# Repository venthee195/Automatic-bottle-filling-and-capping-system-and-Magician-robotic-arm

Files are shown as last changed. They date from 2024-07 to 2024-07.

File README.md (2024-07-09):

<p align="center">
 <h1 align="center">Design and build a bottle processing system using S7-1200 and Magician robotic arm </h1>
</p>

# Introduction
This project involves the design and construction of a system for filling, capping, and arranging glass bottles. The system employs a Magician robotic arm to organize the bottles into a 3x3 grid within a square container. The manufacturing line, equipped with conveyors, pumps, and pneumatic cylinders, is responsible for the filling and capping of the bottles.

The system is controlled by a Siemens SIMATIC S7-1200 CPU 1214C PLC, which also manages the Mitsubishi AC Servo MR-J3 motors. Despite the differences between the two brands, successful integration has been achieved. The PLC is capable of reading the AC Servo’s absolute encoder, enabling the robot to automatically home itself when powered on. This simplifies the initialization process and enhances the overall efficiency of the system.

# System design and construction
Design the whole system, we need a reliable tool that can connect all the parts. That’s why we use SolidWorks 2022 It helps us complete and integrate each stage smoothly.
This part talks about the designs of each part of a system that fills, seals, and caps bottles. We’ll look at the design of the Magician Robotic Arm in Section 3.2.3.
Figure 3-10 presents an overview of the motors’ positions in the system. Each component represents a stage in the production line.

The hardware of the system includes: control devices (PLC, relay), actuators, motors, conveyors, pneumatic cylinders, Camera IMC-3616UC, sensors.

<p align="center">
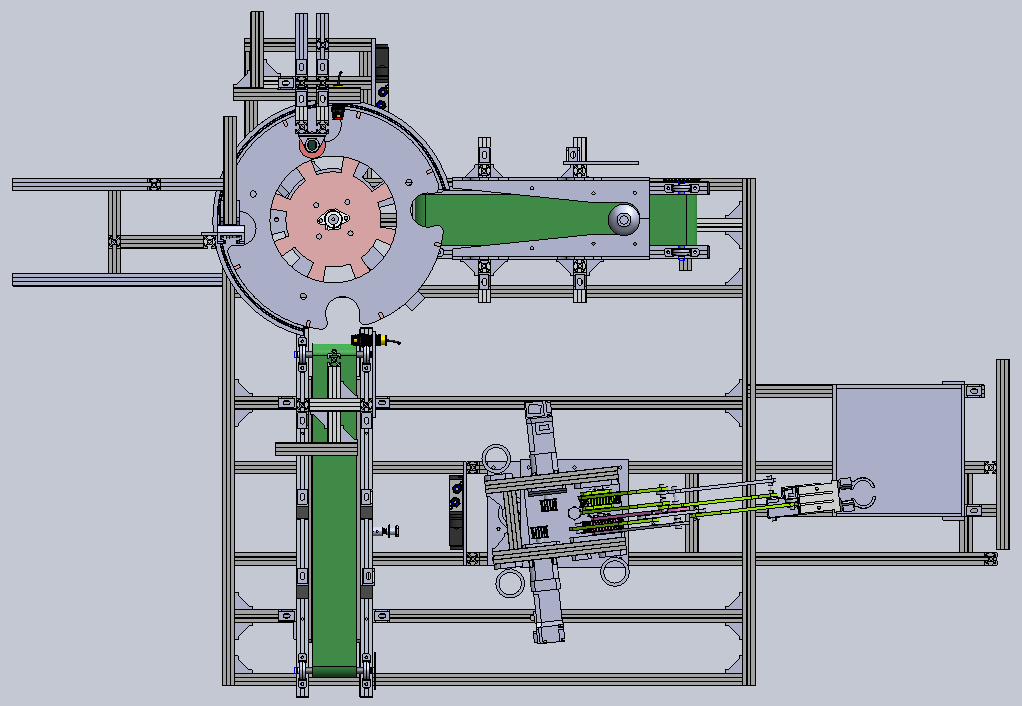
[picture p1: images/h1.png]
  <br/>
  <i>Top view of the system</i>
</p>
<p align="center">
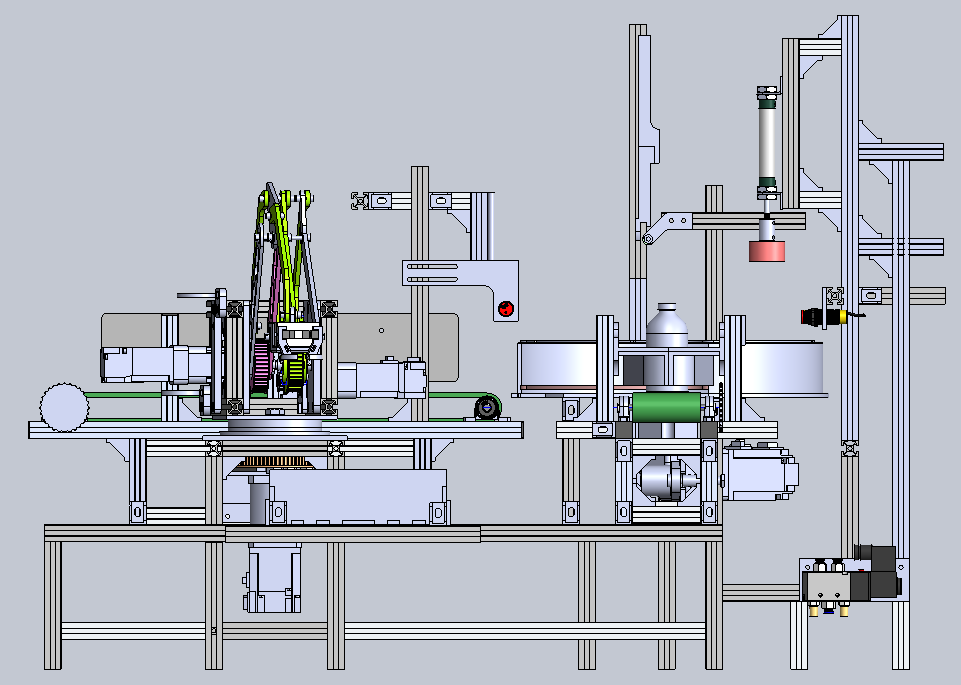
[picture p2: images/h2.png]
  <br/>
  <i>Front view of the system</i>
</p>

Overview of the project:

h3

Design of the Electrical cabinet:

<p align="center">
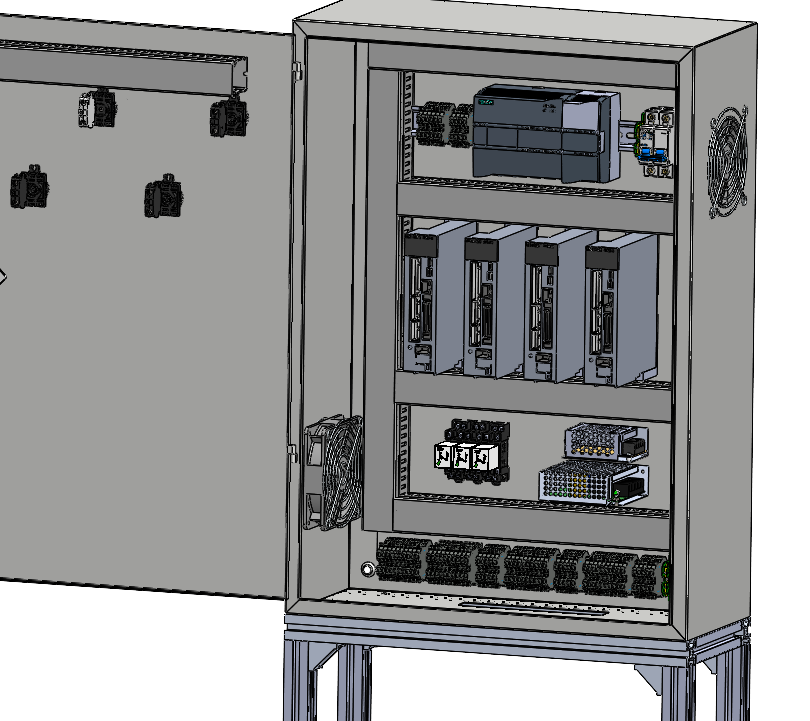
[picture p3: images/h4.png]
  <br/>
  <i> Left side view of cabinet</i>
</p>
<p align="center">
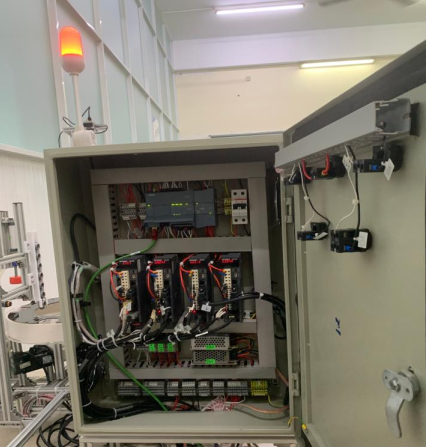
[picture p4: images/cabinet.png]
  <br/>
  <i> Overview of the actual electrical cabinet</i>
</p>
Programmable Logic Controller (PLC): This is the main control unit, responsible for automating various functions.

Circuit Breakers (CB): These are located at the top of the cabinet and protect the circuit from damage caused by excess current from an overload or short circuit.

Servo Drive: Positioned in the middle of the cabinet, this controls the operation of the servo motor.
Intermediate Relays: These devices control the power circuits.

AC to DC Converters: There are two converters, one for 12V and another for 24V, which convert alternating current (AC) to direct current (DC).

Terminal Blocks: These secure and/or terminate multiple wire connections.

Fans: Two 12V fans, each running at 1500 RPM and measuring 12x12 cm, are installed for cooling purposes.

<p align="center">
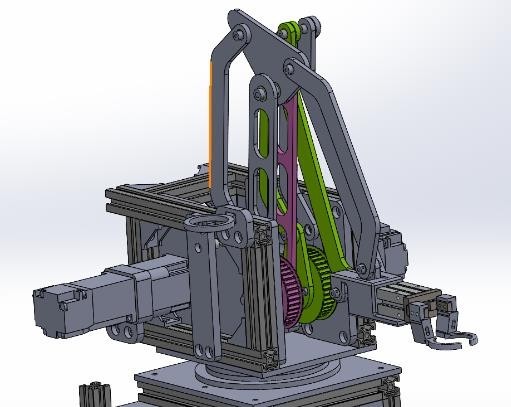
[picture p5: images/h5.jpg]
  <br/>
  <i>Magician Robot Arm model by SolidWorks</i>
</p>

# Control interface design
The interface is designed by the team using the C# programming language.

<p align="center">
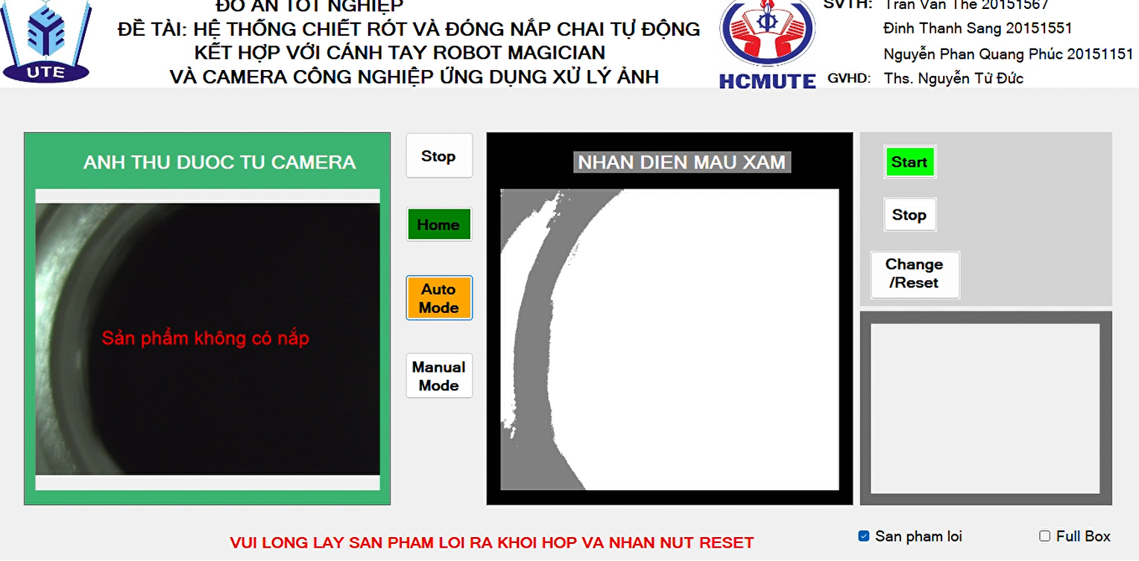
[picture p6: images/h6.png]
  <br/>
  <i>Product interface without cover</i>
</p>

<p align="center">
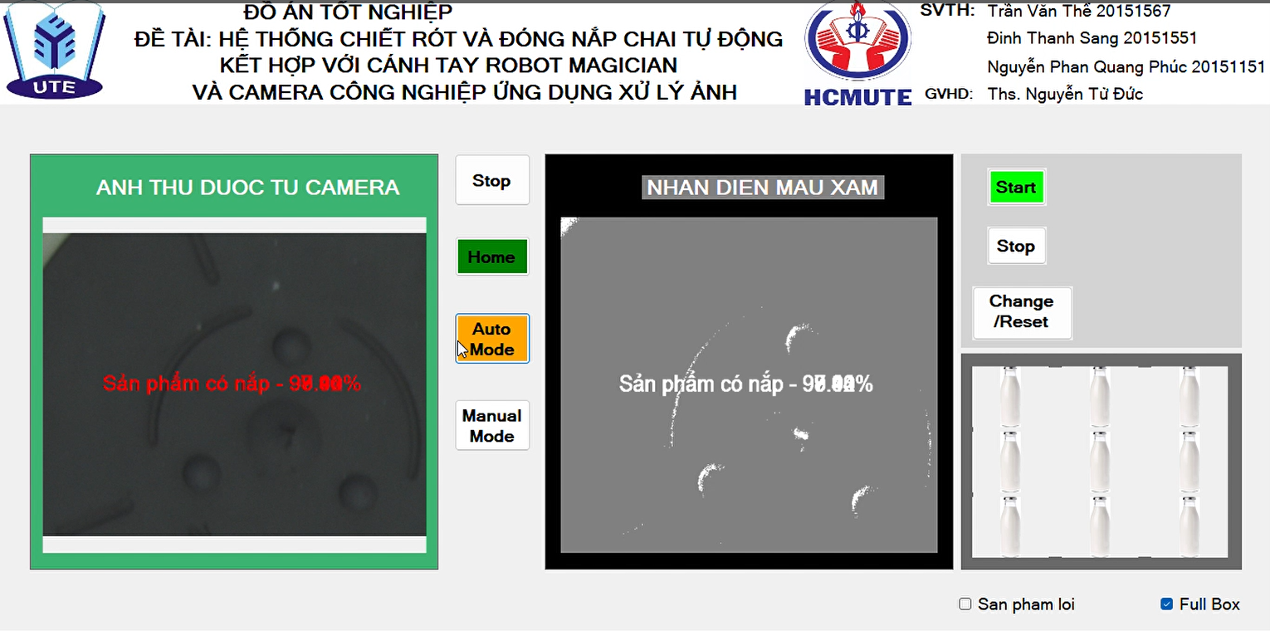
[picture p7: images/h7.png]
  <br/>
  <i>The product interface has a cap and a filled bottle</i>
</p>

# The system wiring diagram

<p align="center">
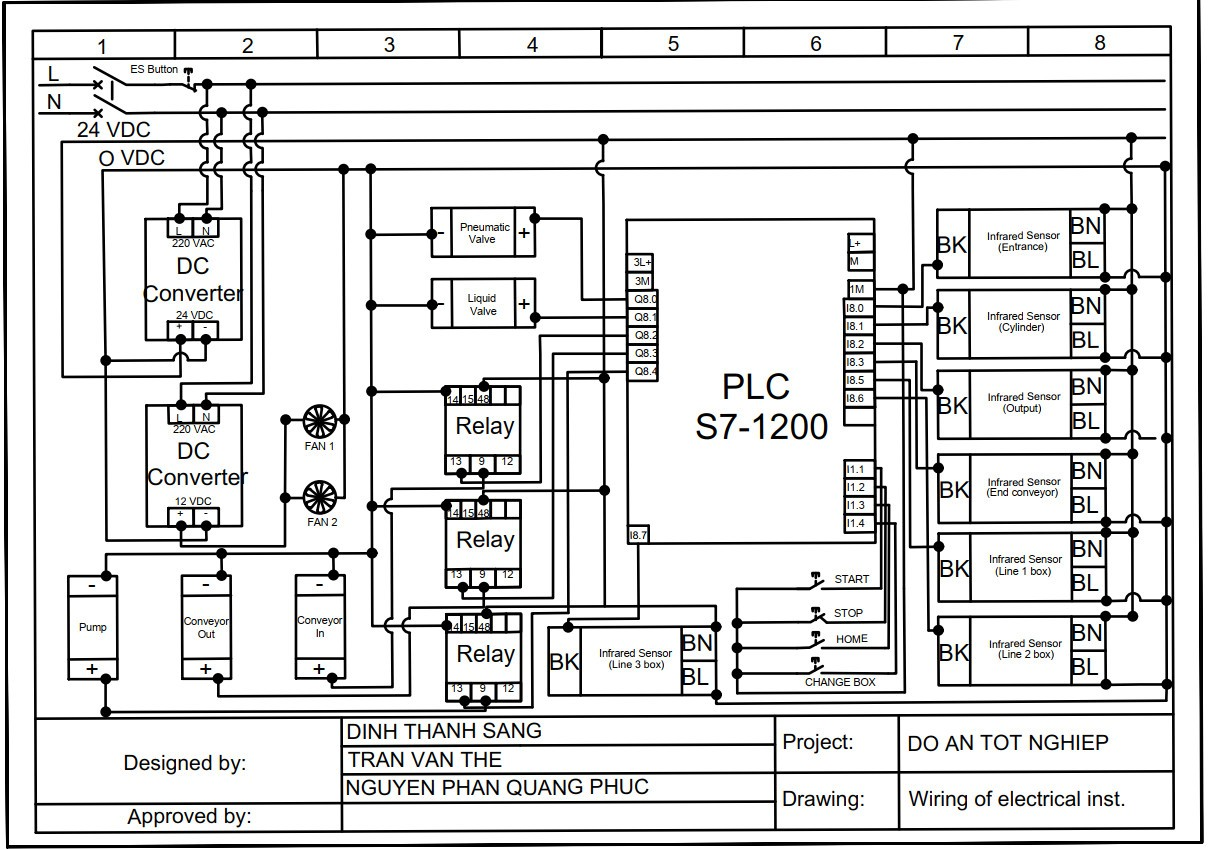
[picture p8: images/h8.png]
  <br/>
  <i>Wiring diagram of other actuators and sensors</i>
</p>

<p align="center">
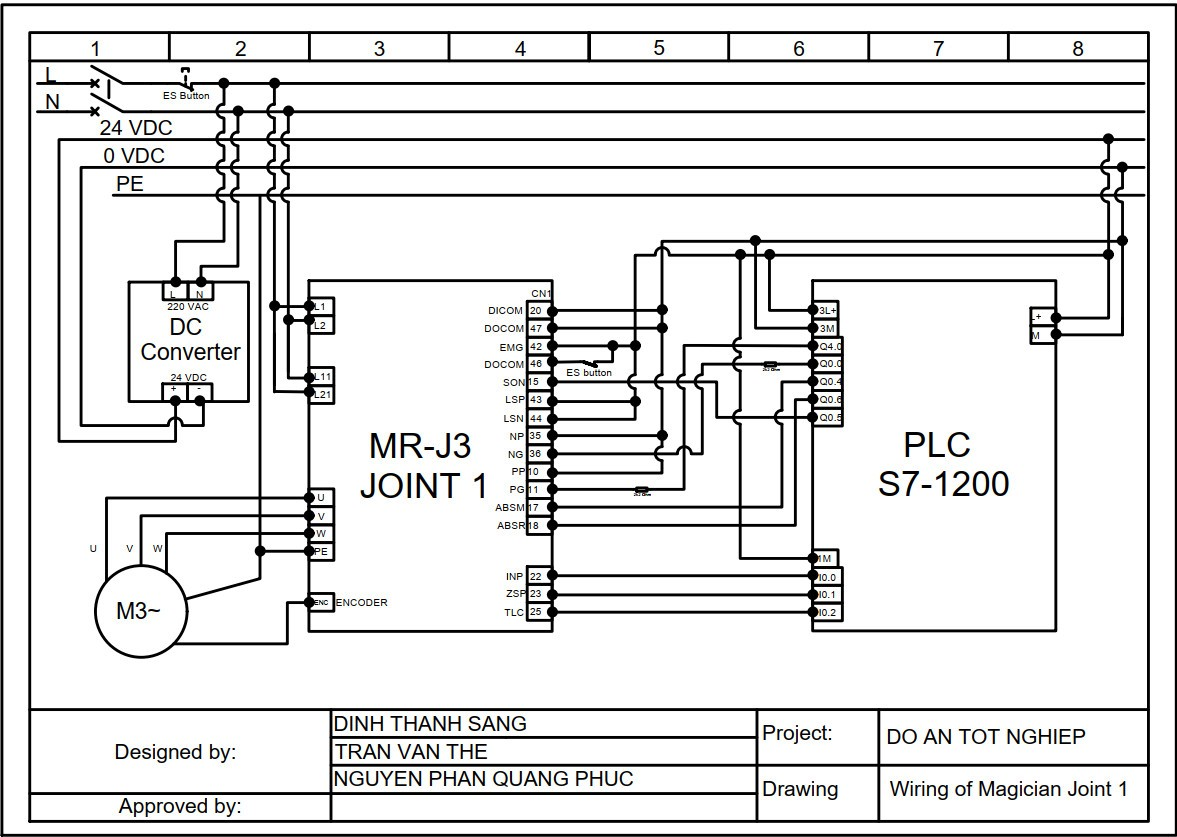
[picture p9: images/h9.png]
  <br/>
  <i>Wiring diagram for Joint 1 of the robotic arm</i>
</p>
<p align="center">
  <img src="images/h10.png width=600><br/>
  <i>Wiring diagram for Joint 2 of the robotic arm</i>
</p>
<p align="center">
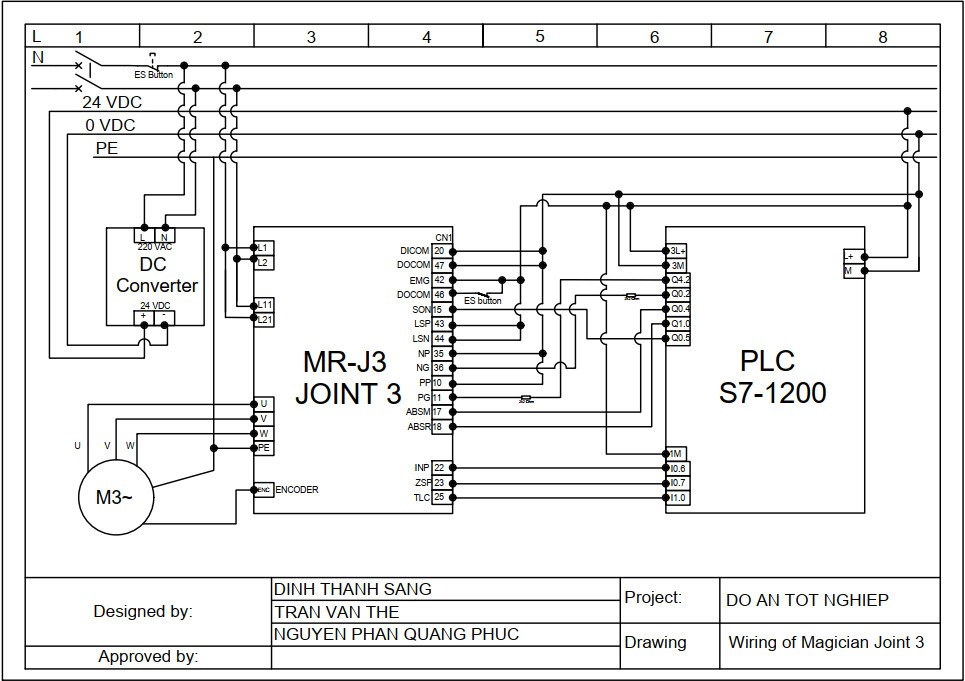
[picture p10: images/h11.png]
  <br/>
  <i>Wiring diagram for Joint 3 of the robotic arm</i>
</p>

 # 
# Experimental results
Initially, empty bottles are placed on the input conveyor and pushed towards the end of the conveyor to fill water into the bottles
<p align="center">
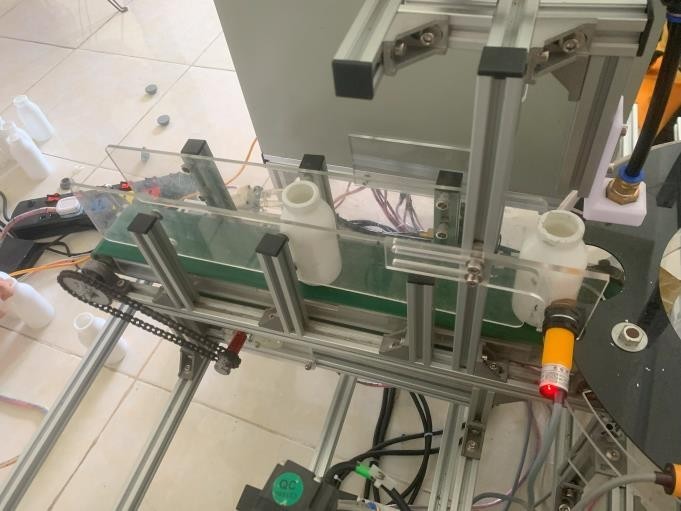
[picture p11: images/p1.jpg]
  <br/>
  <i>Bottles in the input conveyor</i>
</p>

<p align="center">
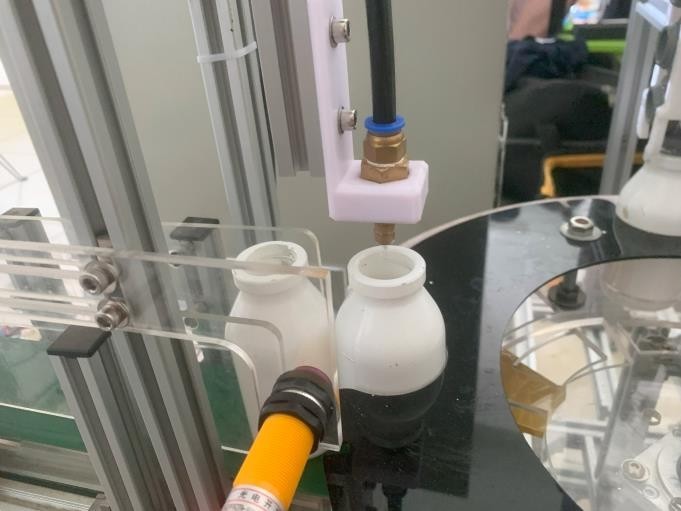
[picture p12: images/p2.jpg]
  <br/>
  <i> Filling water into a bottle</i>
</p>

<p align="center">
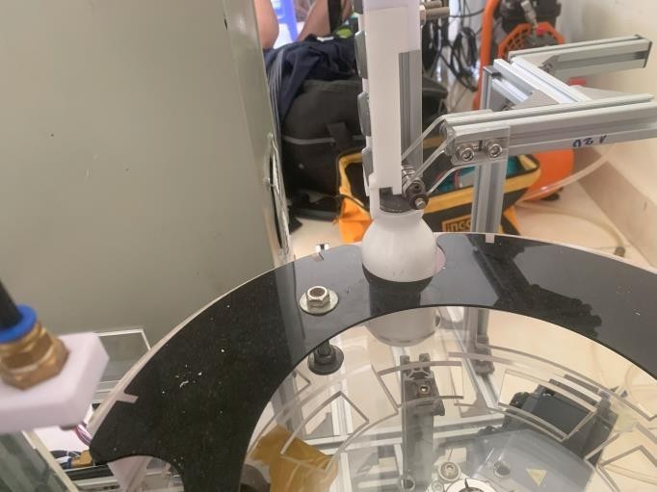
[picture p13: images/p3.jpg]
  <br/>
  <i>Capping a bottle</i>
</p>

<p align="center">
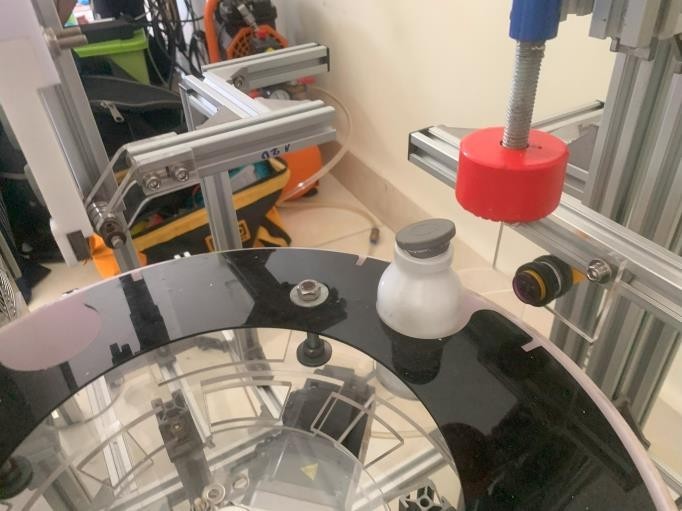
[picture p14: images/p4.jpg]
  <br/>
  <i>Cap before it is capped</i>
</p>
<p align="center">
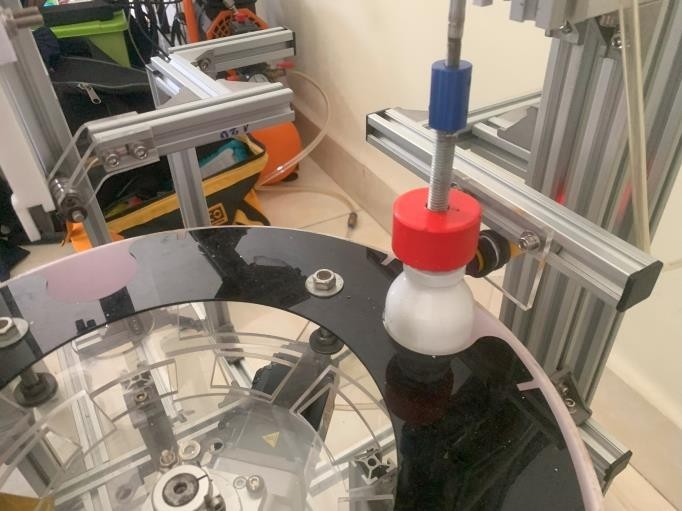
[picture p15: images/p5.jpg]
  <br/>
  <i>Pneumatic cylinder is capping the bottle</i>
</p>

<p align="center">
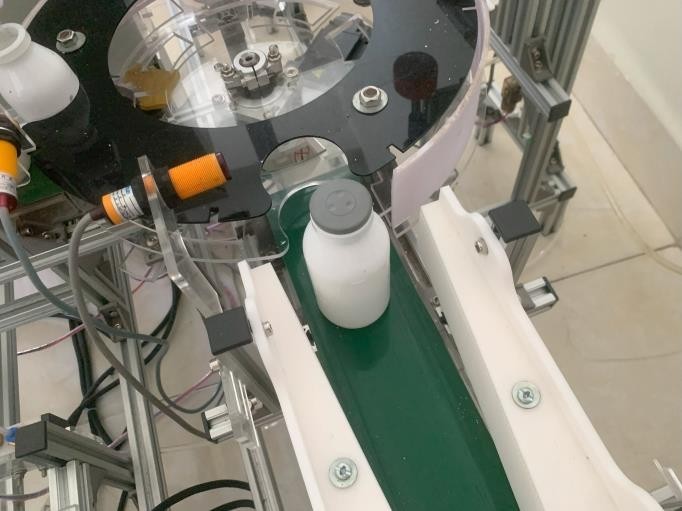
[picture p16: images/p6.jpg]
  <br/>
  <i>Bottles are delivered to the output conveyor</i>
</p>
<p align="center">
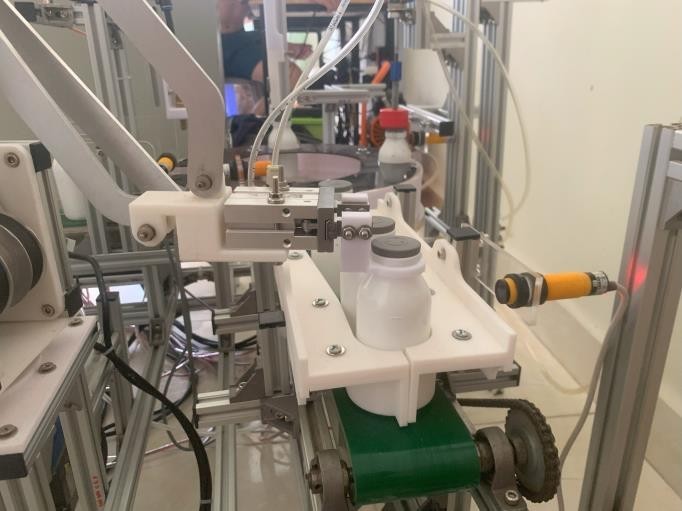
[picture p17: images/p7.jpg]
  <br/>
  <i>A pneumatic cylinder grips bottle</i>
</p>
<p align="center">
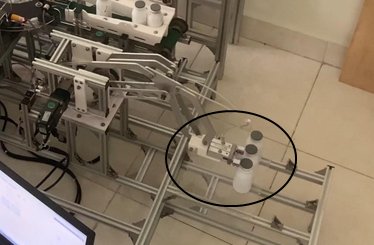
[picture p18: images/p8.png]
  <br/>
  <i>Robotics Arm puts the bottles into the storage</i>
</p>

# Video
For more detail, you can watch the Video show how the system operating: https://youtu.be/p6lmQUOT4Mk?si=QC_-EGU05_skhJYb

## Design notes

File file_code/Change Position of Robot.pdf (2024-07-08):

## Totally Integrated Automation Portal

# Change Position of Robot [FC6]

## Change Position of Robot Properties General

Name | Change Position of Robot | Number | 6 | Type | FC | Language | LAD
Numbering | Automatic

## Information

Title | | Author | Comment | Family
Version | 0.1 | User-defined ID
Name | Data type | Default value | Comment

## Input Output InOut Temp Constant Return

Change Position of Robot | Void

# Network 1: STATE 1 ON

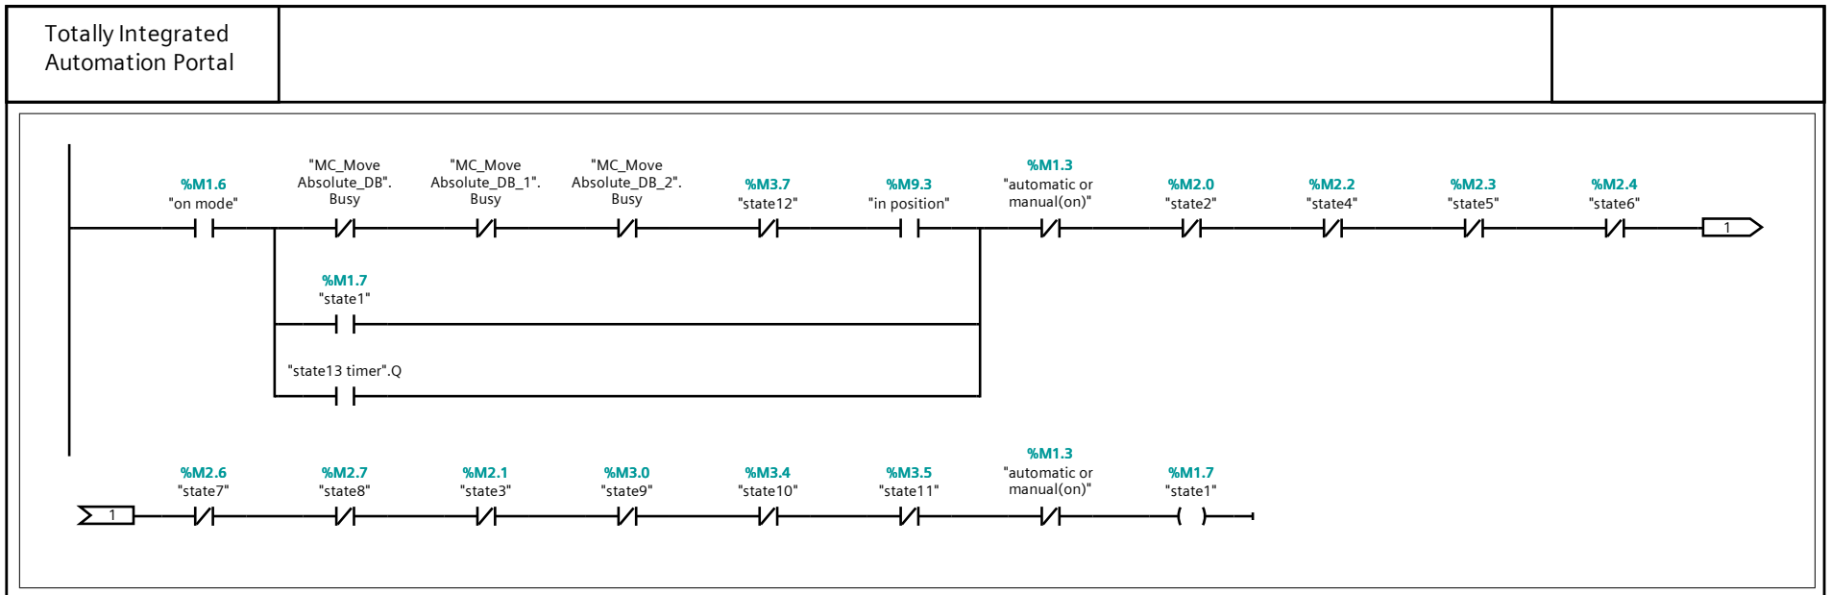
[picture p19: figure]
Automation Portal; "on mode"; "MC_Move Absolute_DB". Busy; "MC_Move Absolute_DB_1". Busy; "MC_Move Absolute_DB_2".; Busy; "state12"; "in position"; "automatic or; manual(on)"; "state2"; "state4"; "state5"; "state6"; "state7"; "state8"; "state3"; "state9"; "state10"; "state11"; "state1"; "state13 timer".Q

# Network 2: Vi tri cua state1

MOVE

MOVE

MOVE

"state1"

%M1.7

450.0
"px"

%MD100

0.0
"py"

%MD104

30.0
"pz"

%MD108

EN
IN

ENO

OUT1

EN
IN

ENO

OUT1

EN
IN

ENO

OUT1

EN
IN

ENO

OUT1

EN
IN

ENO

OUT1

EN
IN

ENO

# OUT1 Network 3:

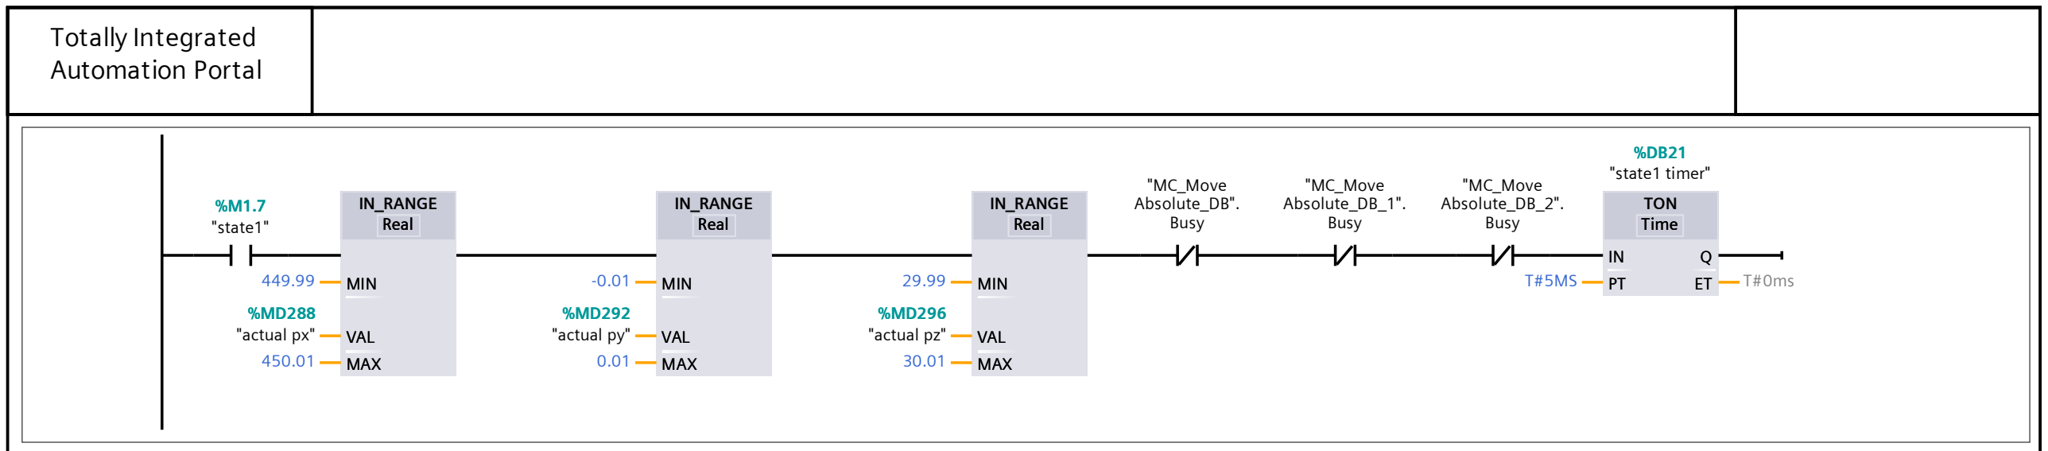
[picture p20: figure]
Automation Portal; IN_RANGE Real; TON; "state1"; Time; "actual px"; "actual py"; "actual pz"; "MC_Move Absolute_DB". Busy; "MC_Move Absolute_DB_1". Busy; "MC_Move Absolute_DB_2". Busy; "state1 timer"; %DB21 MIN; T#0ms VAL MAX; Real; MIN; VAL MAX; Time MIN
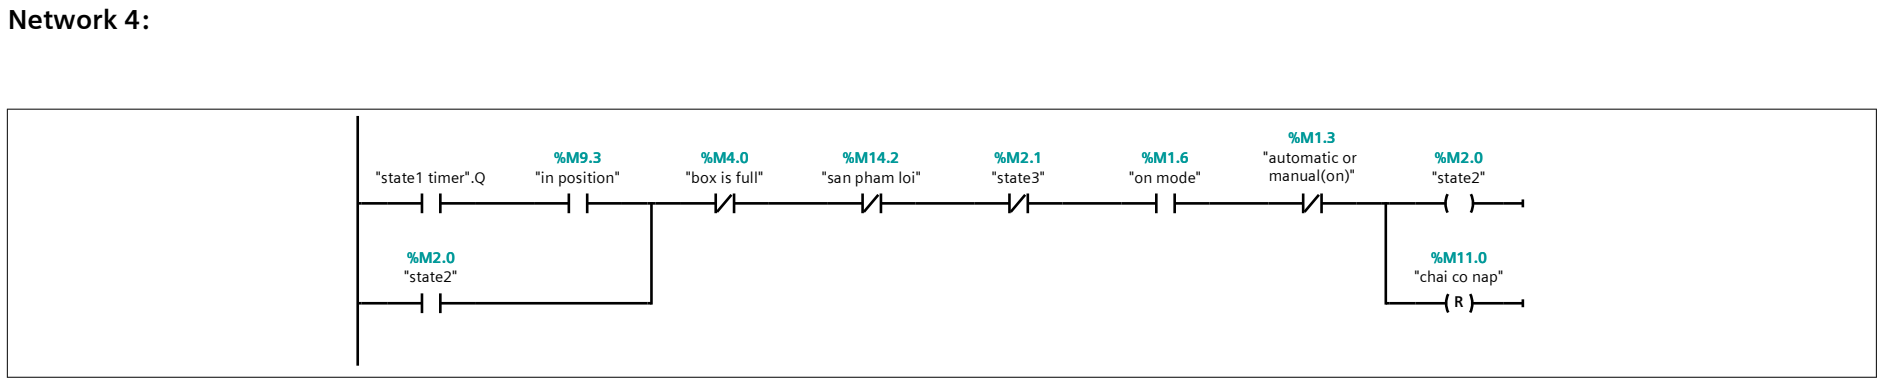
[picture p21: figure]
Network 4:; "state1 timer".Q; "in position"; "box is full"; "san pham loi"; "state3"; "on mode"; "automatic or; manual(on)"; "state2"; "chai co nap"

# Network 5:

## Automation Portal

MOVE

MOVE

MOVE

"state2"

%M2.0

"bottle on
conveyor px"

%MD474
"px"

%MD100

"bottle on
conveyor py"

%MD478
"py"

%MD104

130.0
"pz"

%MD108

EN

IN

ENO

OUT1

EN

IN

ENO

OUT1

EN
IN

ENO

OUT1

EN

IN

ENO

OUT1

EN

IN

ENO

OUT1

EN
IN

ENO

# OUT1 Network 6:

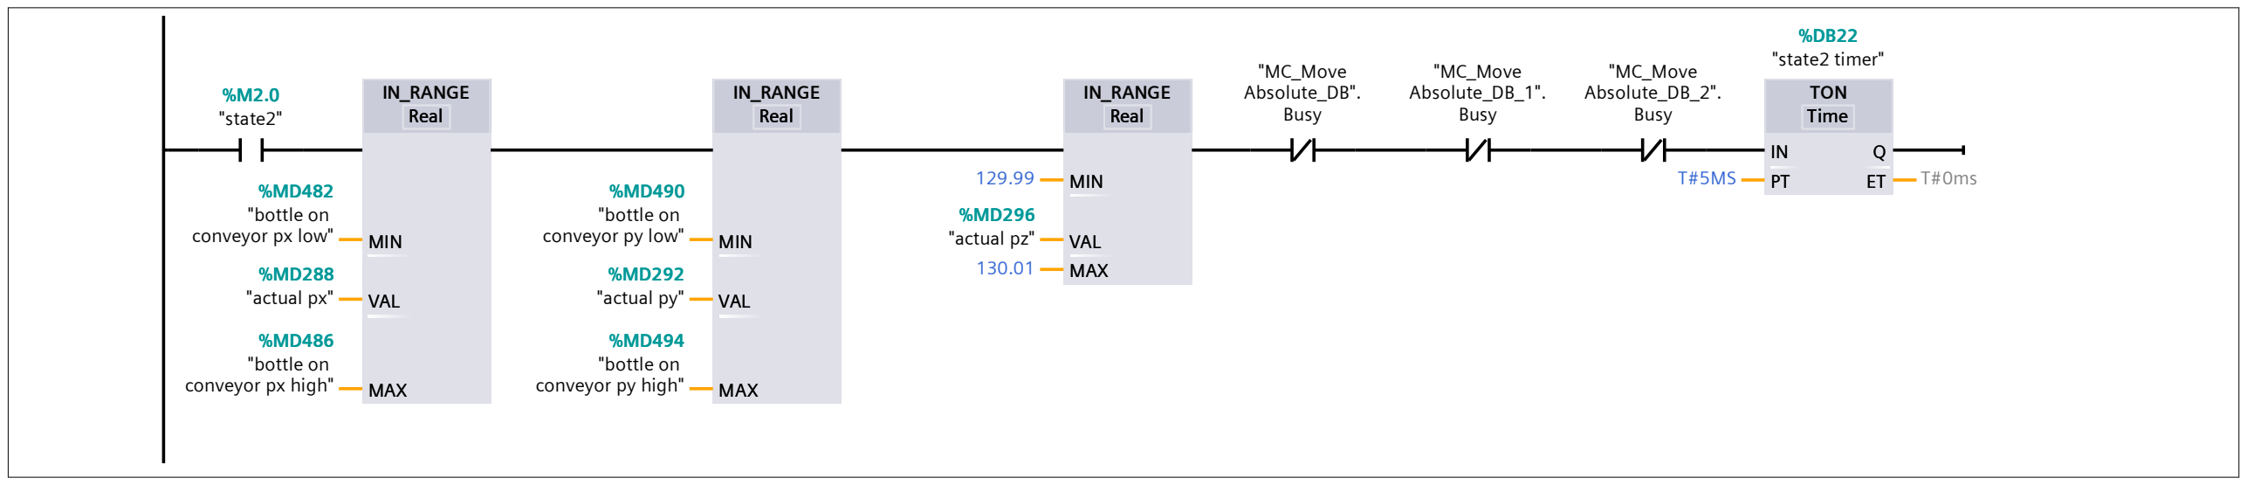
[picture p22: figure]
IN_RANGE Real; TON; "state2"; Time; "bottle on conveyor px low"; "actual px"; "bottle on conveyor px high"; "bottle on conveyor py low"; "actual py"; "bottle on conveyor py high"; "actual pz"; "MC_Move Absolute_DB". Busy; "MC_Move Absolute_DB_1". Busy; "MC_Move Absolute_DB_2". Busy; "state2 timer"; T#0ms MIN; VAL MAX; Real; MIN; Time MIN

# Network 7:

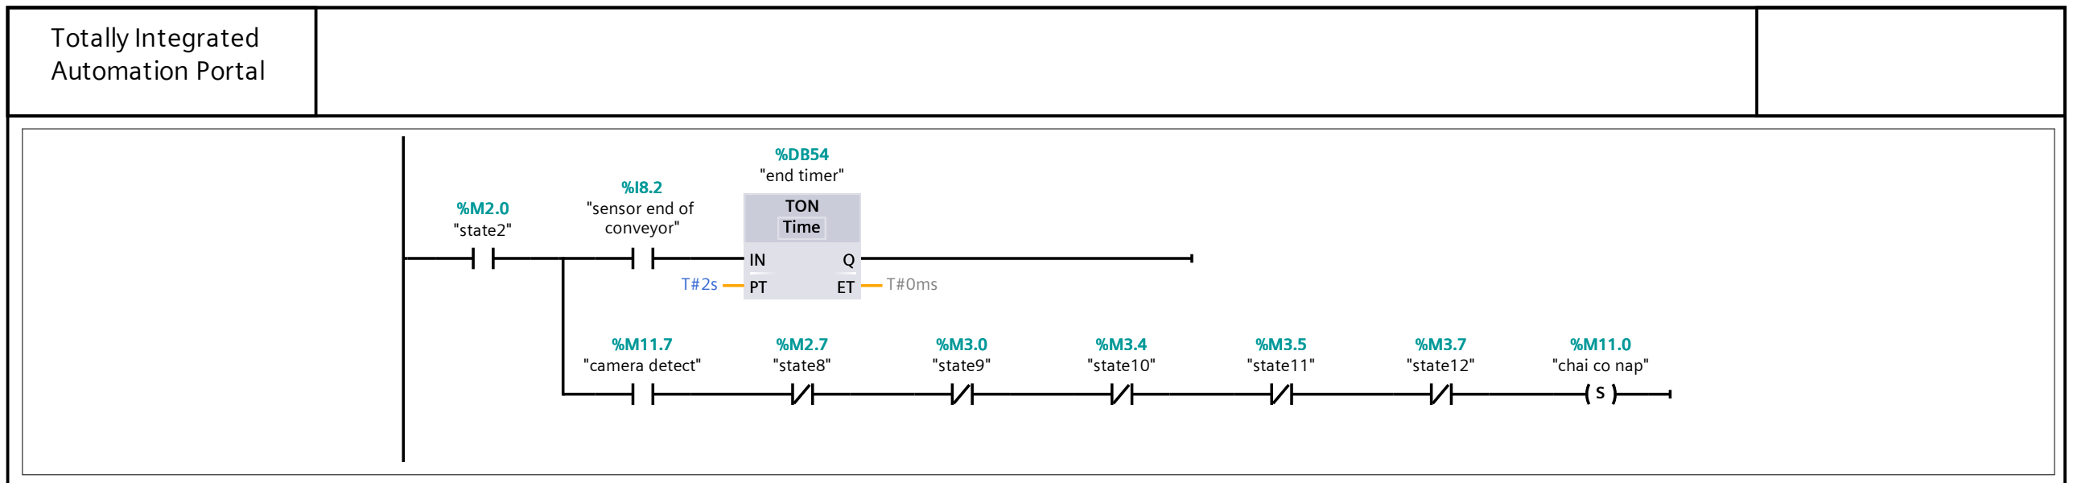
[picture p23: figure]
Automation Portal; TON Time; "state2"; "sensor end of; conveyor"; "end timer"; "camera detect"; "state8"; "state9"; "state10"; "state11"; "state12"; "chai co nap"; Time

# Network 8:

"state2 timer".Q "in position"

%M9.3
"end timer".Q | "state4"

%M2.2
"on mode"
%M1.6 | "automatic or
manual(on)"

%M1.3

"state3"

%M2.1

"state3"

%M2.1

# Network 9:

## Automation Portal

MOVE

MOVE

MOVE

"state3"

%M2.1

"bottle on
conveyor px"

%MD474
"px"

%MD100

"bottle on
conveyor py"

%MD478
"py"

%MD104

115.0
"pz"

%MD108

EN

IN

ENO

OUT1

EN

IN

ENO

OUT1

EN
IN

ENO

OUT1

EN

IN

ENO

OUT1

EN

IN

ENO

OUT1

EN
IN

ENO

# OUT1 Network 10:

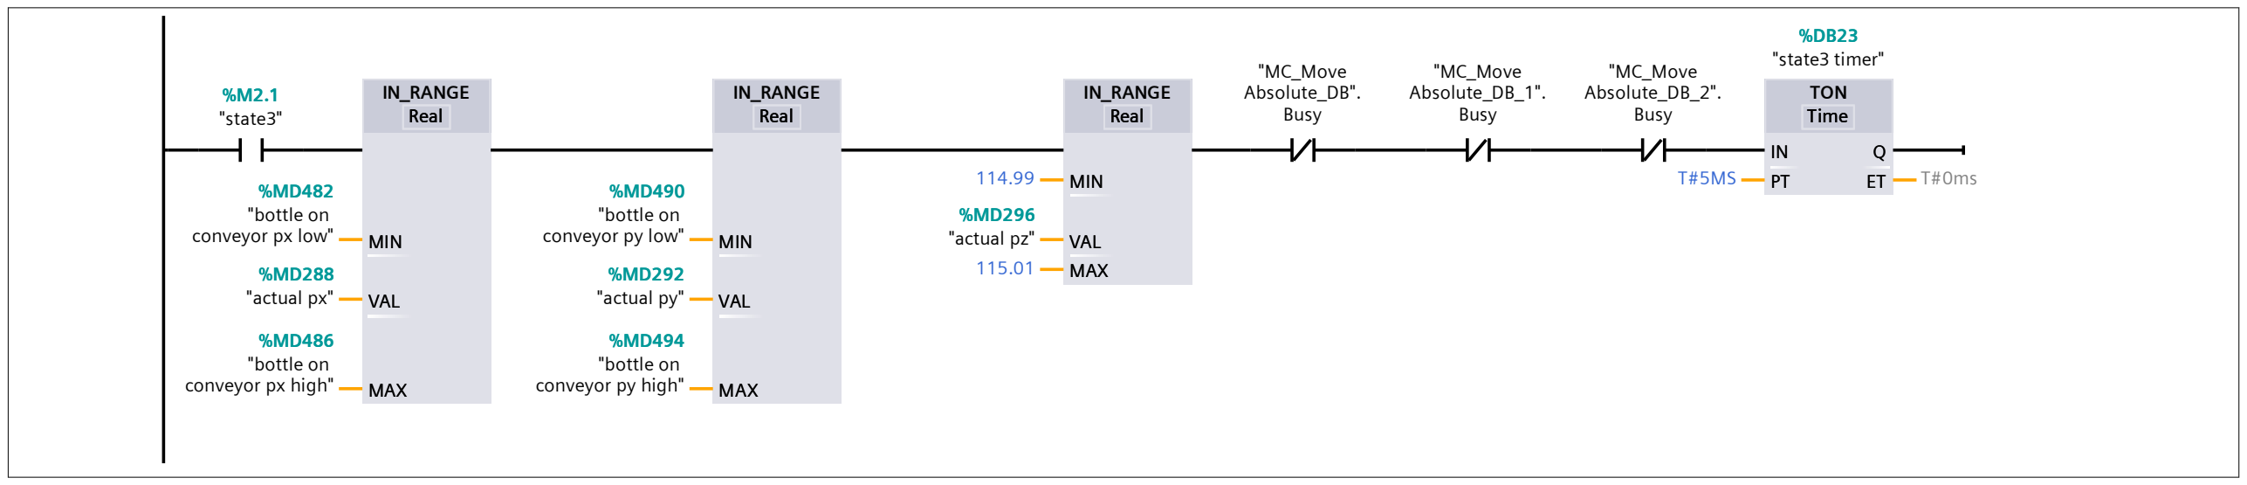
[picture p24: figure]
IN_RANGE Real; TON; "state3"; Time; "bottle on conveyor px low"; "actual px"; "bottle on conveyor px high"; "bottle on conveyor py low"; "actual py"; "bottle on conveyor py high"; "actual pz"; "MC_Move Absolute_DB". Busy; "MC_Move Absolute_DB_1". Busy; "MC_Move Absolute_DB_2". Busy; "state3 timer"; T#0ms MIN; VAL MAX; Real; MIN; Time MIN

# Network 11:

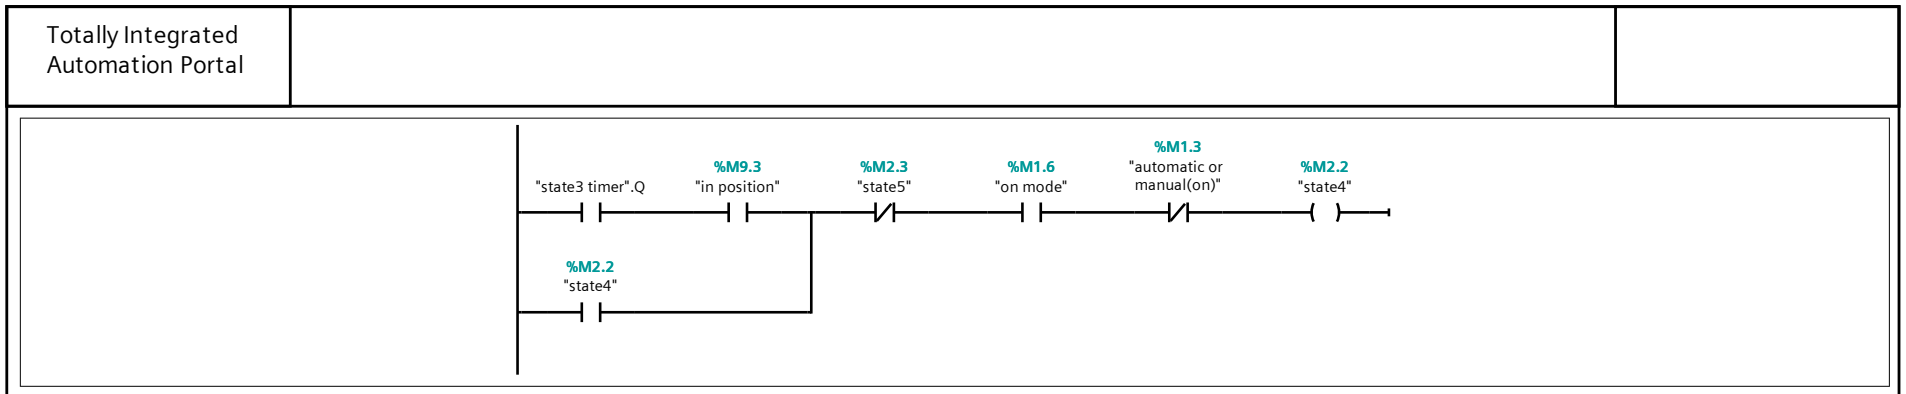
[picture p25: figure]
Automation Portal; "state3 timer".Q; "in position"; "state5"; "on mode"; "automatic or; manual(on)"; "state4"

# Network 12:

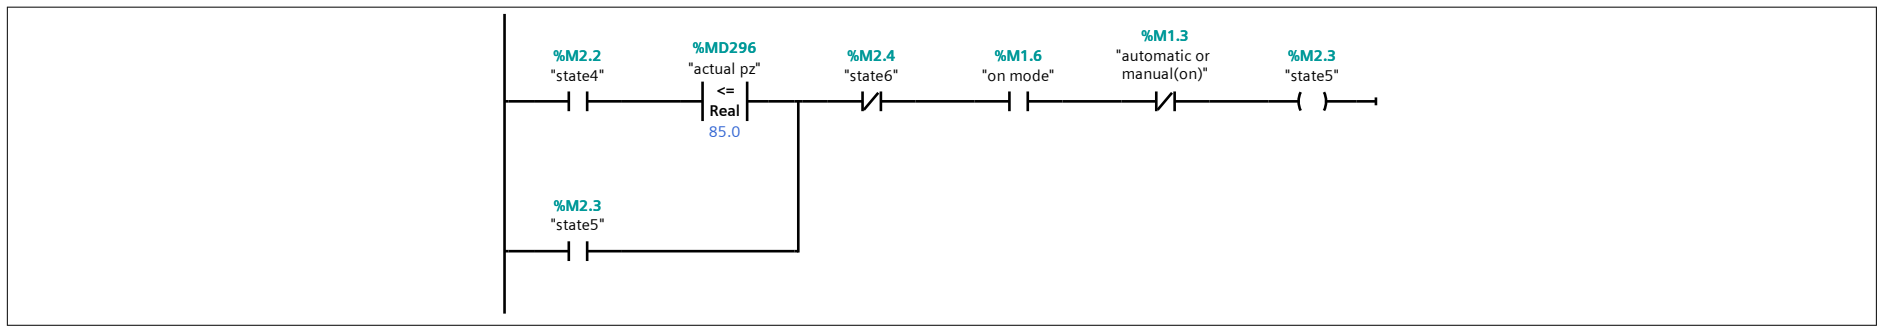
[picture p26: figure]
Real <=; "state4"; "actual pz"; "state6"; "on mode"; "automatic or; manual(on)"; "state5"

# Network 13:

## Automation Portal

MOVE

MOVE

MOVE

"state5"

%M2.3

"bottle on
conveyor px"

%MD474
"px"

%MD100

"bottle on
conveyor py"

%MD478
"py"

%MD104

85.0
"pz"

%MD108

EN

IN

ENO

OUT1

EN

IN

ENO

OUT1

EN
IN

ENO

OUT1

EN

IN

ENO

OUT1

EN

IN

ENO

OUT1

EN
IN

ENO

# OUT1 Network 14:

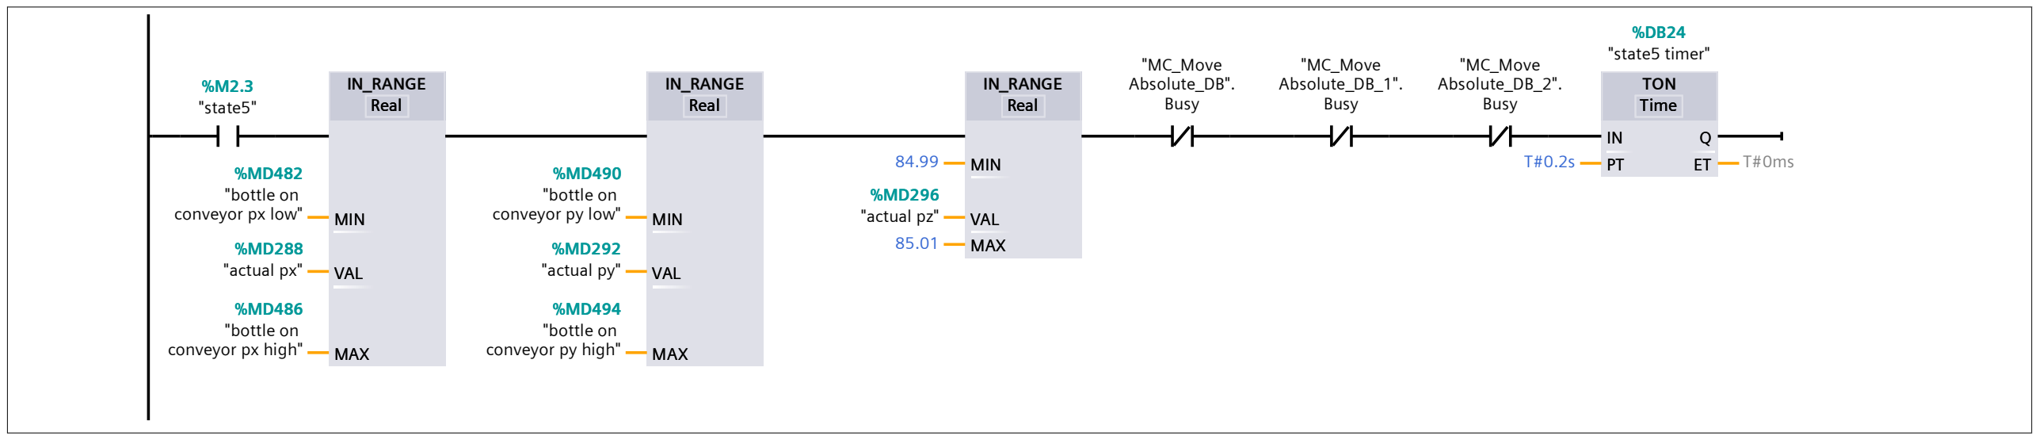
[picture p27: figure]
IN_RANGE Real; TON; "state5"; Time; "bottle on conveyor px low"; "actual px"; "bottle on conveyor px high"; "bottle on conveyor py low"; "actual py"; "bottle on conveyor py high"; "actual pz"; "MC_Move Absolute_DB". Busy; "MC_Move Absolute_DB_1". Busy; "MC_Move Absolute_DB_2". Busy; "state5 timer"; T#0ms MIN; VAL MAX; Real; MIN; Time MIN

# Network 15:

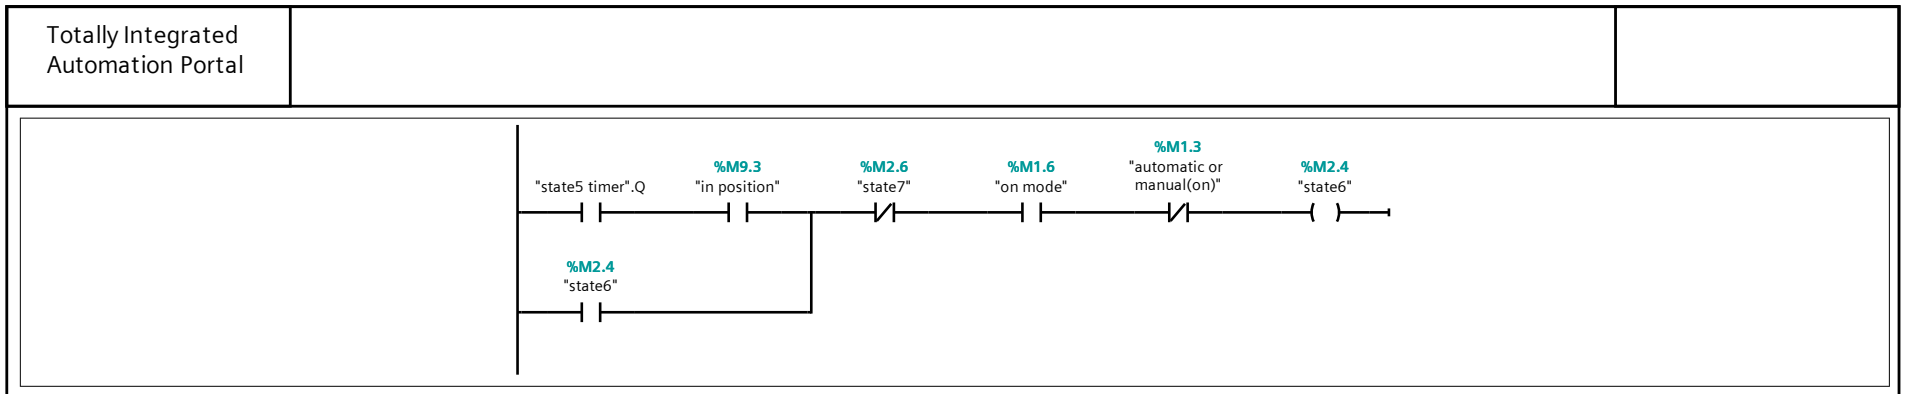
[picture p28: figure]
Automation Portal; "state5 timer".Q; "in position"; "state7"; "on mode"; "automatic or; manual(on)"; "state6"

# Network 16:

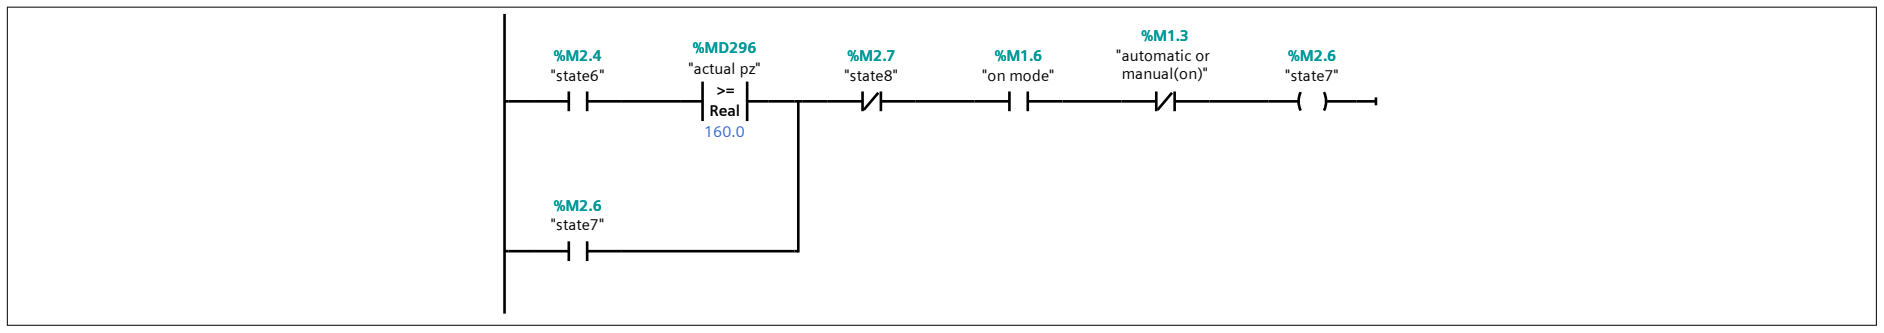
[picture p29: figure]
Real >=; "state6"; "actual pz"; "state8"; "on mode"; "automatic or; manual(on)"; "state7"

# Network 17:

## Automation Portal

MOVE

MOVE

MOVE

"state7"

%M2.6

"array position". "bottle position

x"["bottle
position order"]

"px"

%MD100

"array position". "bottle position

y"["bottle
position order"]

"py"

%MD104

160.0
"pz"

%MD108

EN

IN

ENO

OUT1

EN

IN

ENO

OUT1

EN
IN

ENO

OUT1

EN

IN

ENO

OUT1

EN

IN

ENO

OUT1

EN
IN

ENO
OUT1 Network 18: | ADD

Auto (Real)

SUB
Auto (Real)

"array position". "bottle position

x"["bottle
position order"]

0.01

"bottle position
upper x"
%MD346 | "array position". "bottle position
| x"["bottle position order"]
| 0.01

"bottle position
lower x"

%MD354

EN

IN1
IN2

ENO

OUT

Auto (Real) | EN

IN1
IN2

ENO

OUT

Auto (Real) EN

IN1
IN2

ENO

OUT

Auto (Real) | EN

IN1
IN2

ENO

OUT

Auto (Real)

# Network 19:

Automation Portal | ADD

Auto (Real)

SUB
Auto (Real)

"array position". "bottle position

y"["bottle
position order"]

0.01

"bottle position
upper y"
%MD350 | "array position". "bottle position
| y"["bottle position order"]
| 0.01

"bottle position
lower y"

%MD358

EN

IN1
IN2

ENO

OUT

Auto (Real) | EN

IN1
IN2

ENO

OUT

Auto (Real) EN

IN1
IN2

ENO

OUT

Auto (Real) | EN

IN1
IN2

ENO

OUT

Auto (Real)

# Network 20:

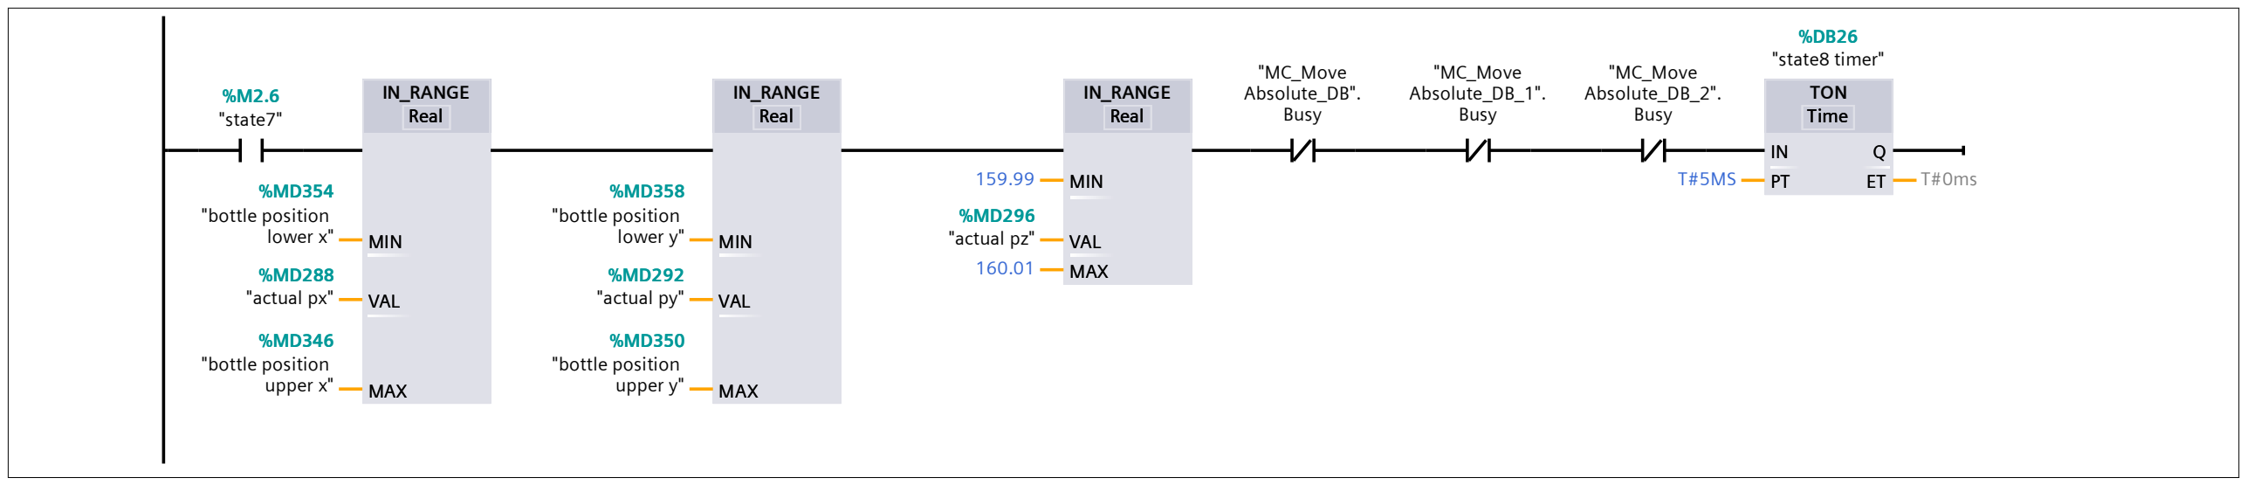
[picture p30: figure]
IN_RANGE Real; TON; "state7"; Time; "bottle position lower x"; "actual px"; "bottle position upper x"; "bottle position lower y"; "actual py"; "bottle position upper y"; "actual pz"; "MC_Move Absolute_DB". Busy; "MC_Move Absolute_DB_1". Busy; "MC_Move Absolute_DB_2". Busy; "state8 timer"; T#0ms MIN; VAL MAX; Real; MIN; Time MIN

# Network 21:

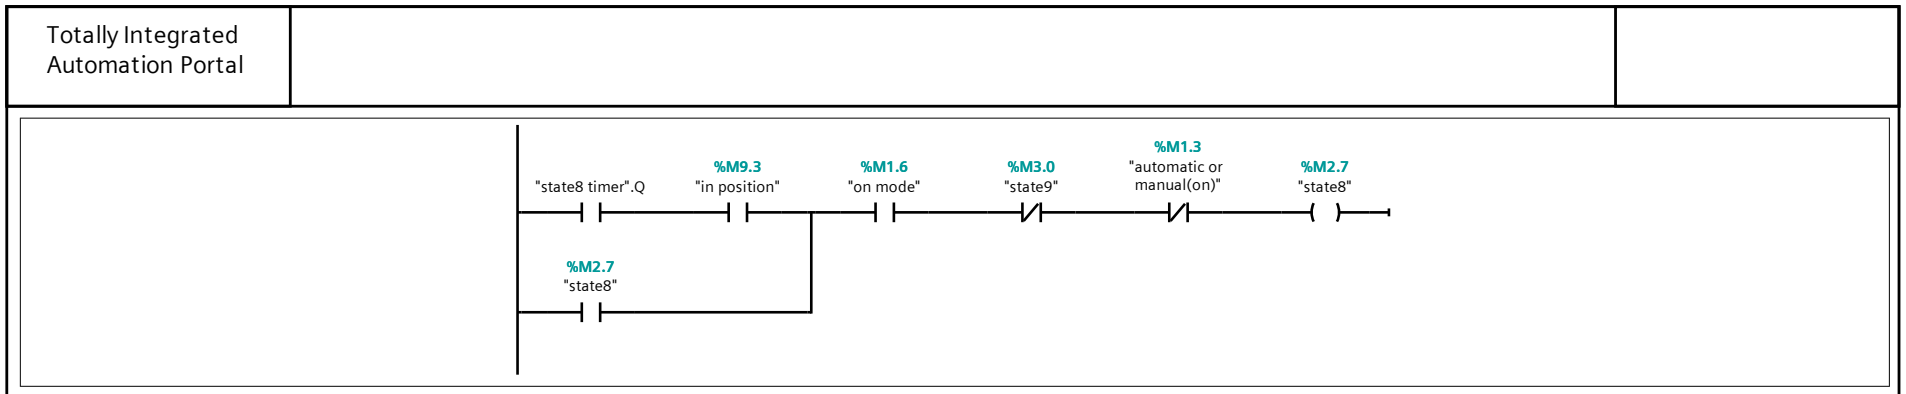
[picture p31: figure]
Automation Portal; "state8 timer".Q; "in position"; "on mode"; "state9"; "automatic or; manual(on)"; "state8"

# Network 22:

## Automation Portal

MOVE

MOVE

MOVE

MOVE

MOVE

MOVE

"state8"

%M2.7
"chai co nap"

%M11.0

"array position". "bottle position

x"["bottle
position order"]

"px"

%MD100

"chai co nap"

%M11.0

"defective bottle
px"

%MD500
"px"

%MD100

"defective bottle
py"

%MD504
"py"

%MD104

80.0
"pz"

%MD108

"array position". "bottle position

y"["bottle
position order"]

"py"

%MD104

80.0
"pz"

%MD108

EN

IN

ENO

OUT1

EN

IN

ENO

OUT1

EN

IN

ENO

OUT1

EN
IN

ENO

OUT1

EN

IN

ENO

OUT1

EN
IN

ENO

OUT1

EN

IN

ENO

OUT1

EN

IN

ENO

OUT1

EN

IN

ENO

OUT1

EN
IN

ENO

OUT1

EN

IN

ENO

OUT1

EN
IN

ENO

OUT1

# Network 23:

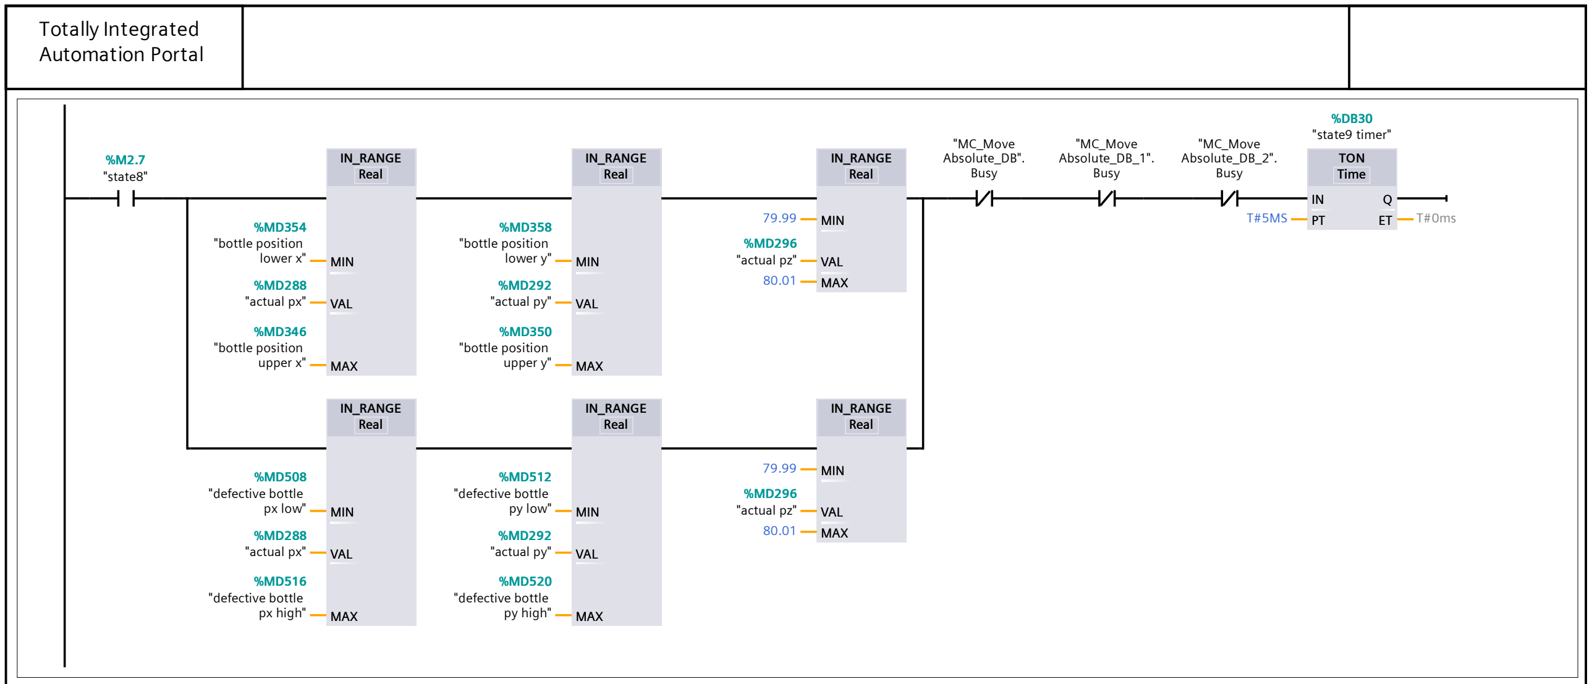
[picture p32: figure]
Automation Portal; IN_RANGE Real; TON Time; "state8"; "bottle position lower x"; "actual px"; "bottle position upper x"; "bottle position lower y"; "actual py"; "bottle position upper y"; "actual pz"; "MC_Move Absolute_DB". Busy; "MC_Move Absolute_DB_1". Busy; "MC_Move Absolute_DB_2". Busy; "state9 timer"; "defective bottle px low"; "defective bottle px high"; "defective bottle py low"; "defective bottle py high"; 80.01 MIN; VAL MAX; Real; MIN; Time MIN; Real MIN

# Network 24:

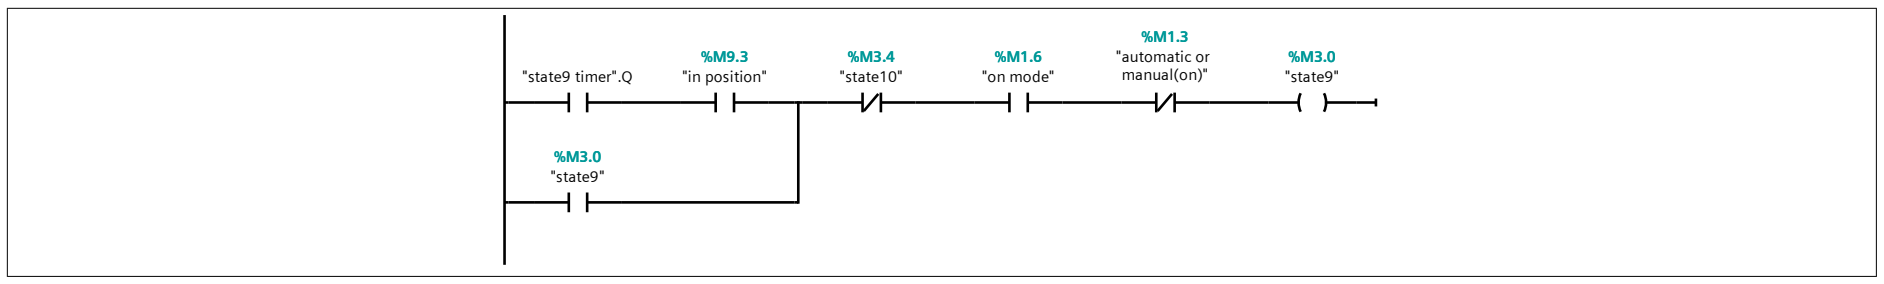
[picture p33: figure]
"state9 timer".Q; "in position"; "state10"; "on mode"; "automatic or; manual(on)"; "state9"

## Automation Portal

# Network 25:

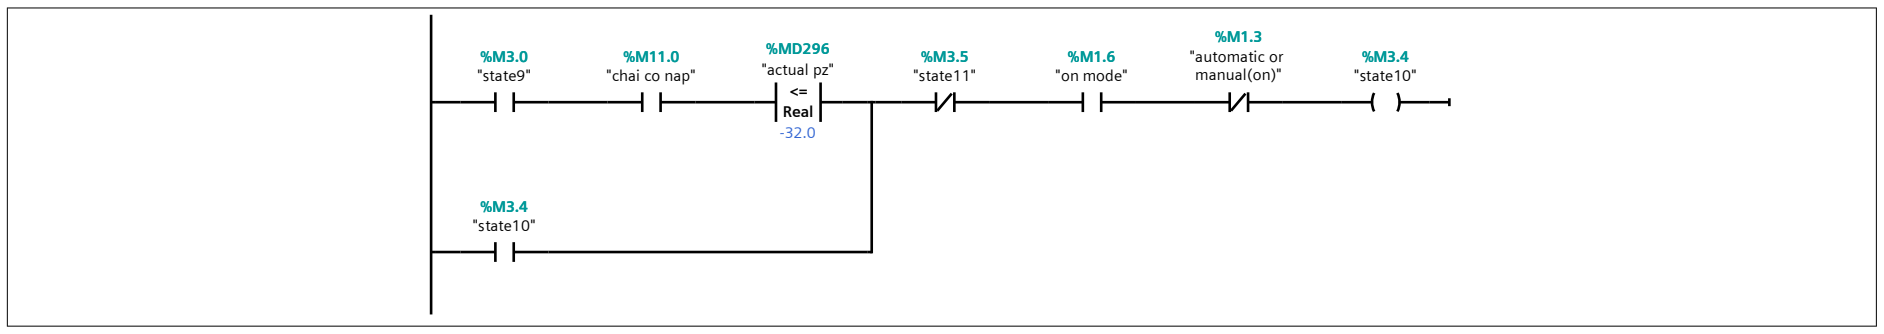
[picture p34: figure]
Real <=; "state9"; "chai co nap"; "actual pz"; "state11"; "on mode"; "automatic or; manual(on)"; "state10"

# Network 26:

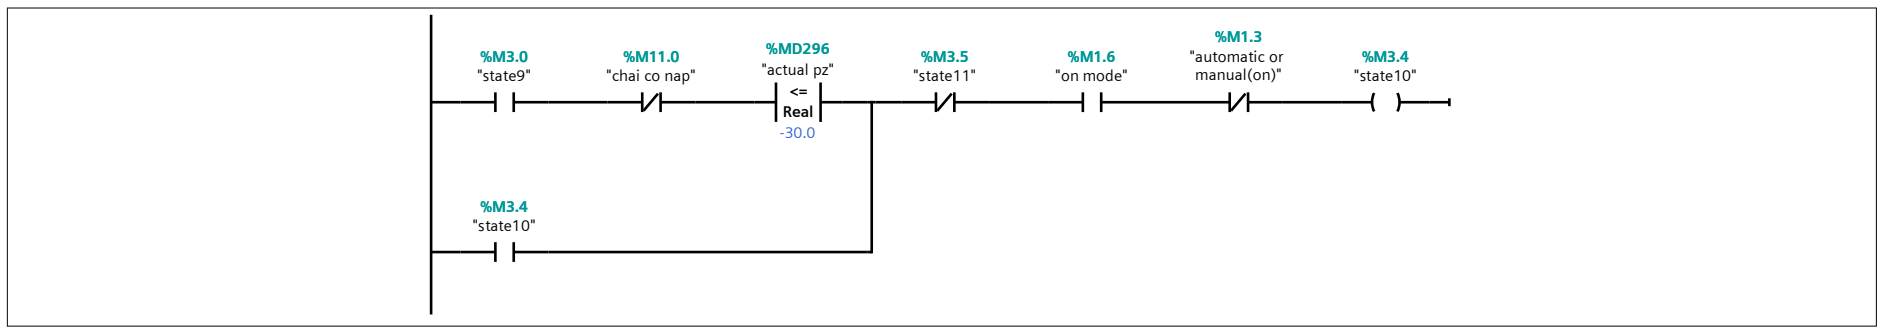
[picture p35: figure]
Real <=; "state9"; "chai co nap"; "actual pz"; "state11"; "on mode"; "automatic or; manual(on)"; "state10"

# Network 27:

## Automation Portal

MOVE

MOVE

MOVE

MOVE

MOVE

MOVE

"state10"

%M3.4
"chai co nap"

%M11.0

"array position". "bottle position

x"["bottle
position order"]

"px"

%MD100

"chai co nap"

%M11.0

"defective bottle
px"

%MD500
"px"

%MD100

"defective bottle
py"

%MD504
"py"

%MD104

-30.0
"pz"

%MD108

"array position". "bottle position

y"["bottle
position order"]

"py"

%MD104

-32.0
"pz"

%MD108

EN

IN

ENO

OUT1

EN

IN

ENO

OUT1

EN

IN

ENO

OUT1

EN
IN

ENO

OUT1

EN

IN

ENO

OUT1

EN
IN

ENO

OUT1

EN

IN

ENO

OUT1

EN

IN

ENO

OUT1

EN

IN

ENO

OUT1

EN
IN

ENO

OUT1

EN

IN

ENO

OUT1

EN
IN

ENO

OUT1

# Network 28:

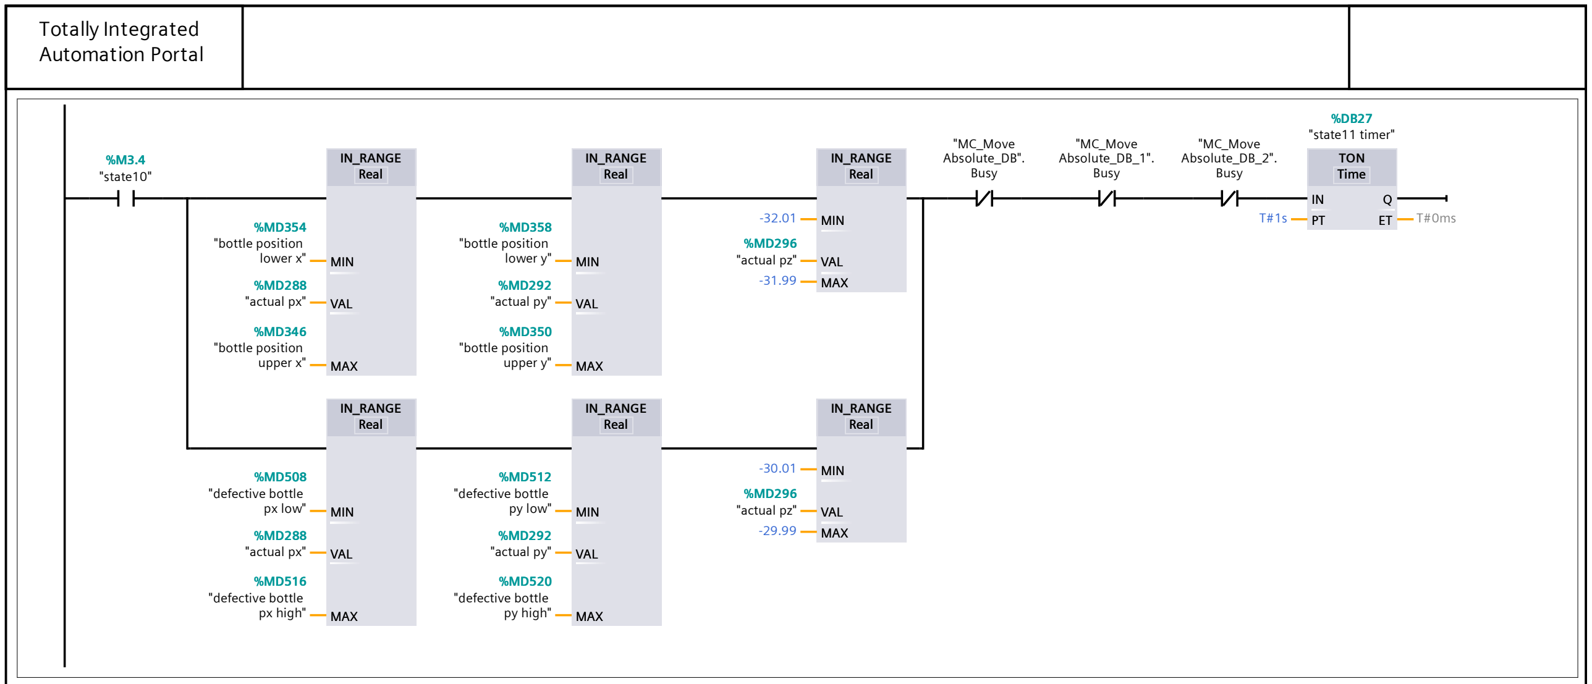
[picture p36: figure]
Automation Portal; IN_RANGE Real; TON Time; "state10"; "bottle position lower x"; "actual px"; "bottle position upper x"; "bottle position lower y"; "actual py"; "bottle position upper y"; "actual pz"; "MC_Move Absolute_DB". Busy; "MC_Move Absolute_DB_1". Busy; "MC_Move Absolute_DB_2". Busy; "state11 timer"; "defective bottle px low"; "defective bottle px high"; "defective bottle py low"; "defective bottle py high"; -29.99 MIN; VAL MAX; Real; MIN; Time MIN; Real MIN

# Network 29:

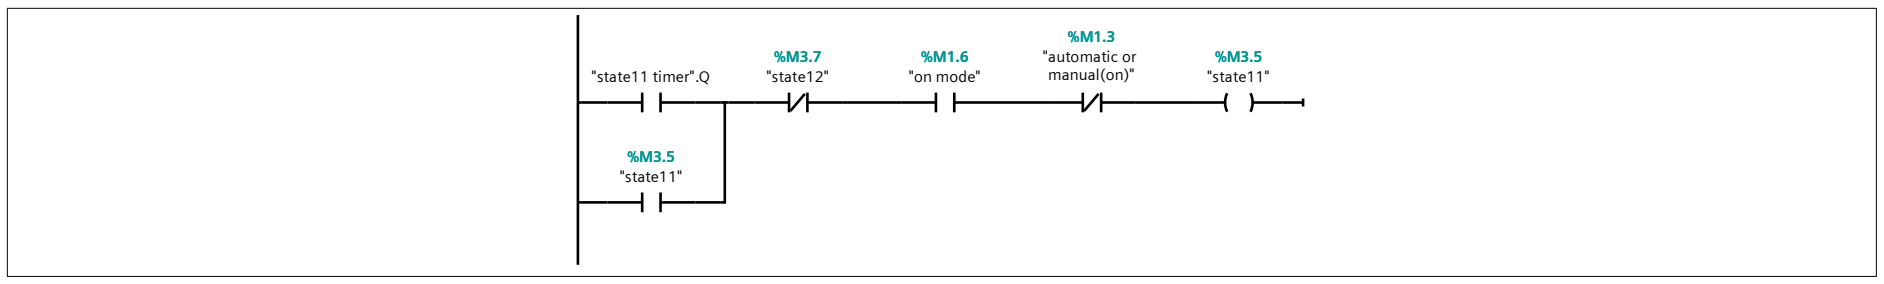
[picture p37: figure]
"state11 timer".Q; "state12"; "on mode"; "automatic or; manual(on)"; "state11"

## Automation Portal

# Network 30:

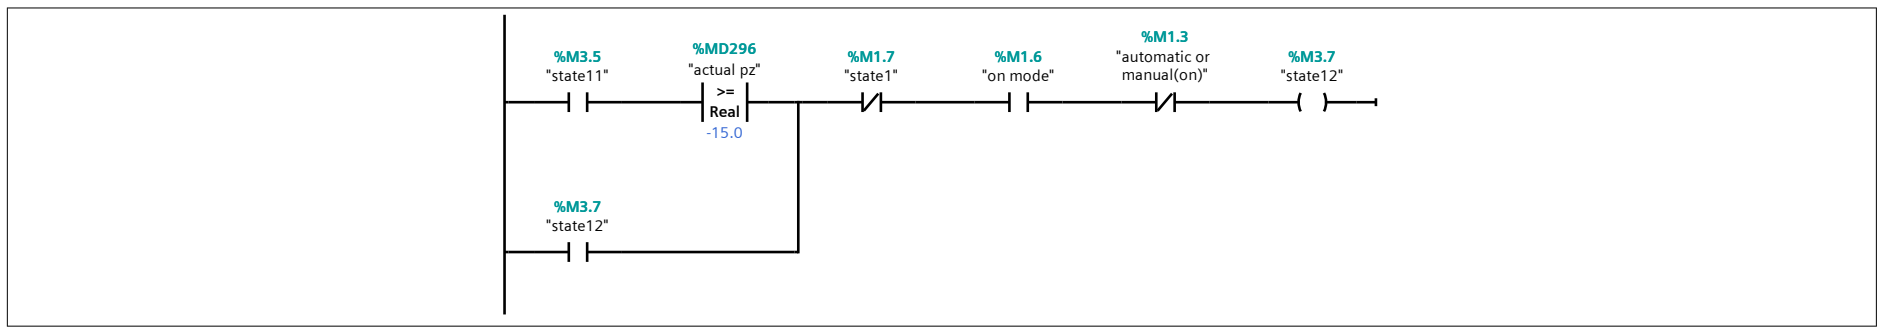
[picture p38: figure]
Real >=; "state11"; "actual pz"; "state1"; "on mode"; "automatic or; manual(on)"; "state12"

# Network 31:

## Automation Portal

MOVE

MOVE

MOVE

MOVE

MOVE

MOVE

"state12"

%M3.7
"chai co nap"

%M11.0

"array position". "bottle position

x"["bottle
position order"]

"px"

%MD100

"chai co nap"

%M11.0

"defective bottle
px"

%MD500
"px"

%MD100

"defective bottle
py"

%MD504
"py"

%MD104

-10.0
"pz"

%MD108

"array position". "bottle position

y"["bottle
position order"]

"py"

%MD104

-15.0
"pz"

%MD108

EN

IN

ENO

OUT1

EN

IN

ENO

OUT1

EN

IN

ENO

OUT1

EN
IN

ENO

OUT1

EN

IN

ENO

OUT1

EN
IN

ENO

OUT1

EN

IN

ENO

OUT1

EN

IN

ENO

OUT1

EN

IN

ENO

OUT1

EN
IN

ENO

OUT1

EN

IN

ENO

OUT1

EN
IN

ENO

OUT1

# Network 32:

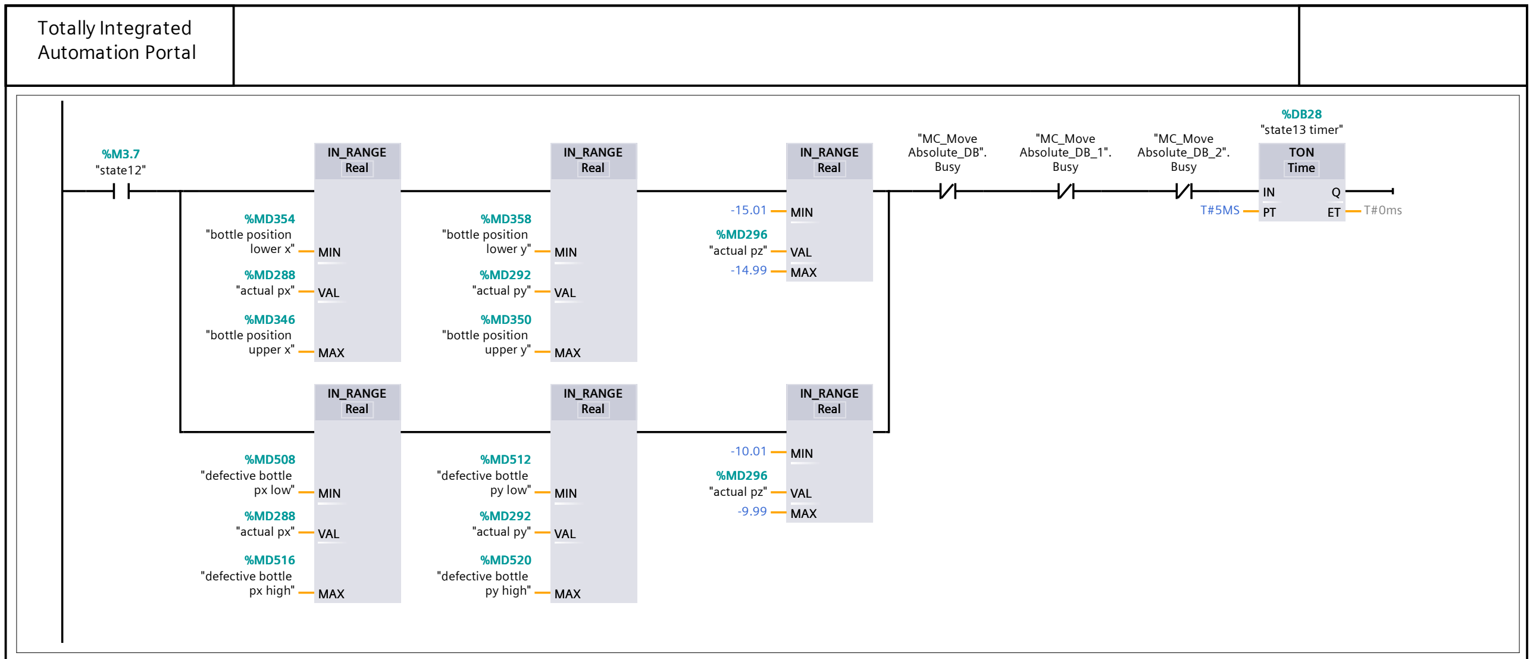
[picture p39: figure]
Automation Portal; IN_RANGE Real; TON Time; "state12"; "bottle position lower x"; "actual px"; "bottle position upper x"; "bottle position lower y"; "actual py"; "bottle position upper y"; "actual pz"; "MC_Move Absolute_DB". Busy; "MC_Move Absolute_DB_1". Busy; "MC_Move Absolute_DB_2". Busy; "state13 timer"; "defective bottle px low"; "defective bottle px high"; "defective bottle py low"; "defective bottle py high"; -9.99 MIN; VAL MAX; Real; MIN; Time MIN; Real MIN

# Network 33:

"state12"; "chai co nap"; "san pham loi"

# Network 34:

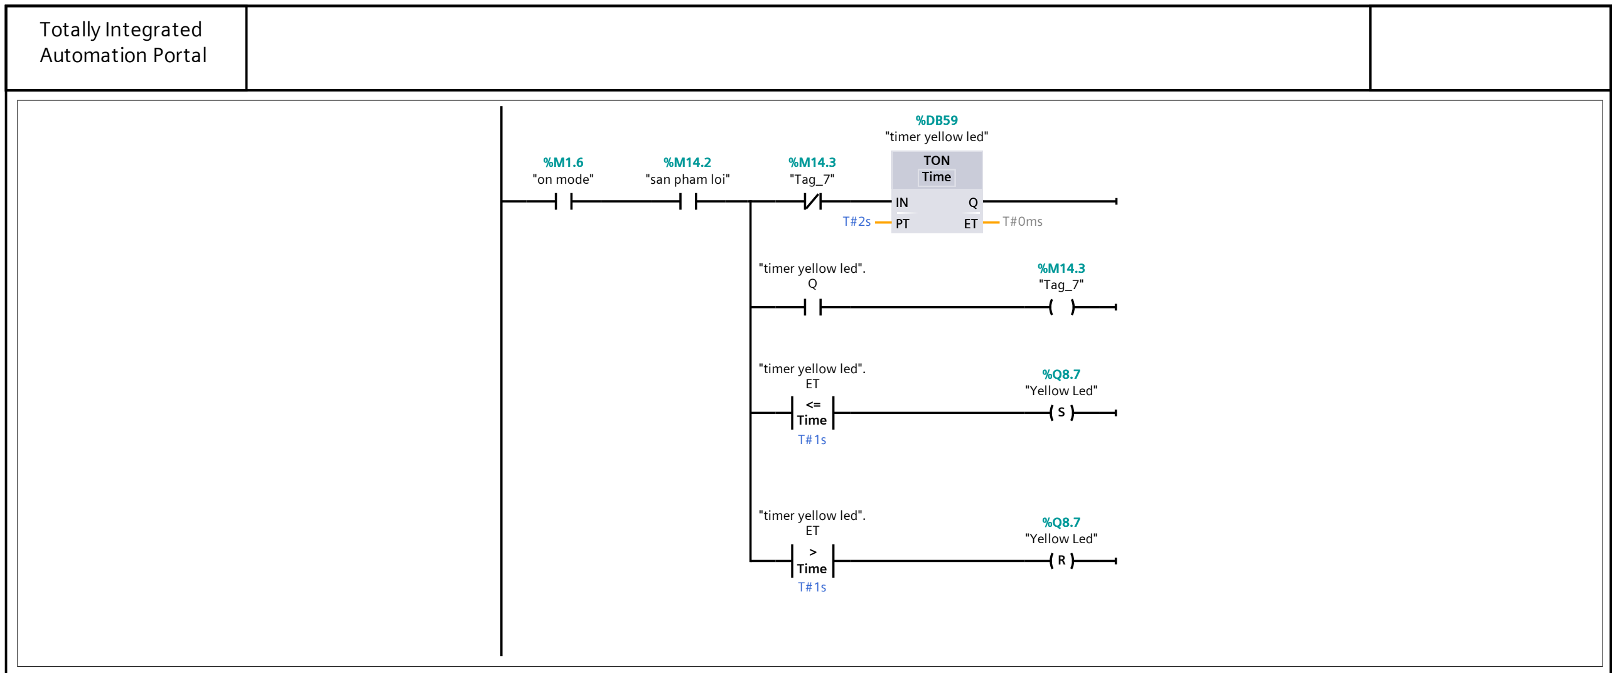
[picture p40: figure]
Automation Portal; TON Time; Time <=; Time >; "on mode"; "san pham loi"; "Tag_7"; "timer yellow led"; "timer yellow led". Q "Tag_7"; "timer yellow led". ET; "Yellow Led"; Time

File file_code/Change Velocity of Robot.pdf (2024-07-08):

## Totally Integrated Automation Portal

# fix_plc / PLC_1 [CPU 1214C DC/DC/DC] / Program blocks

# Change Velocity of Robot [FC7]

## Change Velocity of Robot Properties General

Name | Change Velocity of Robot | Number | 7 | Type | FC | Language | LAD
Numbering | Automatic

## Information

Title | | Author | Comment | Family
Version | 0.1 | User-defined ID

## Change Velocity of Robot

Name | Data type | Default value | Comment

## Input Output InOut Temp Constant Return

Change Velocity of Robot | Void

# Network 1:

"state4" | MOVE

%M2.2

-50.0
"zdot"

%MD264

EN
IN

ENO

OUT1

# Network 2:

## Automation Portal

"state6" | MOVE

%M2.4

100.0
"zdot"

%MD264

EN
IN

ENO

OUT1

# Network 3:

"state9" | MOVE

%M3.0

-80.0
"zdot"

%MD264

EN
IN

ENO

OUT1

# Network 4:

"state11" | MOVE

%M3.5

80.0
"zdot"

%MD264

EN
IN

ENO

OUT1

# Network 5:

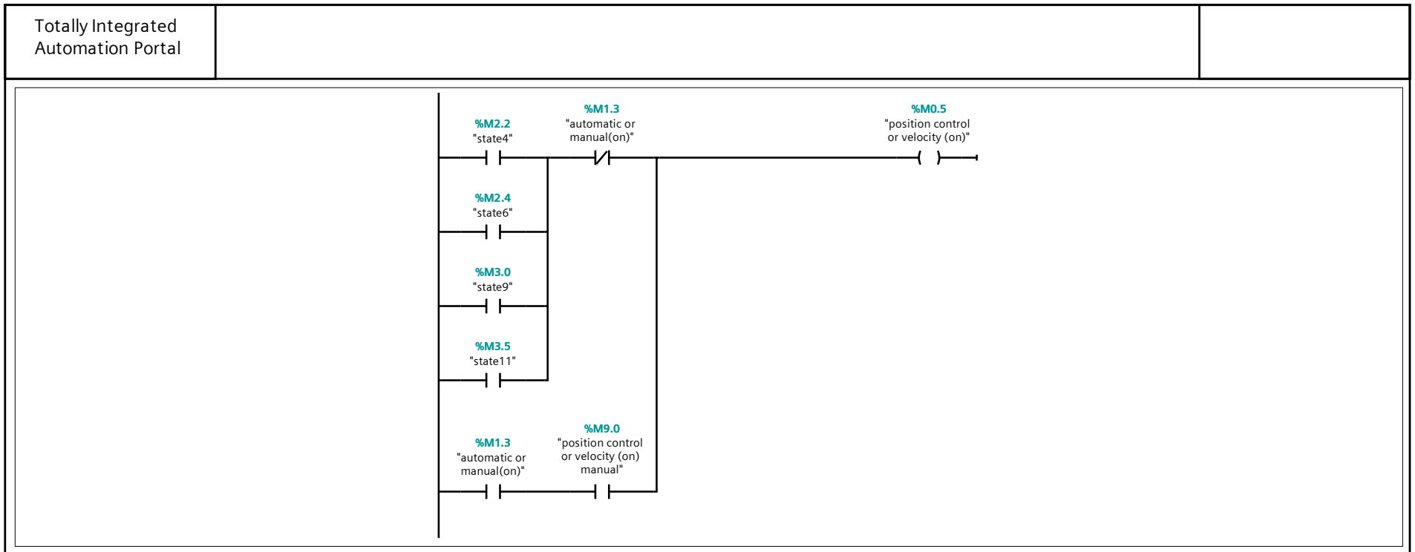
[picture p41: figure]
Automation Portal; "state4"; "automatic or; manual(on)"; "position control or velocity (on)"; "state6"; "state9"; "state11"; "automatic or manual(on)"; "position control; or velocity (on) manual"

# Network 6:

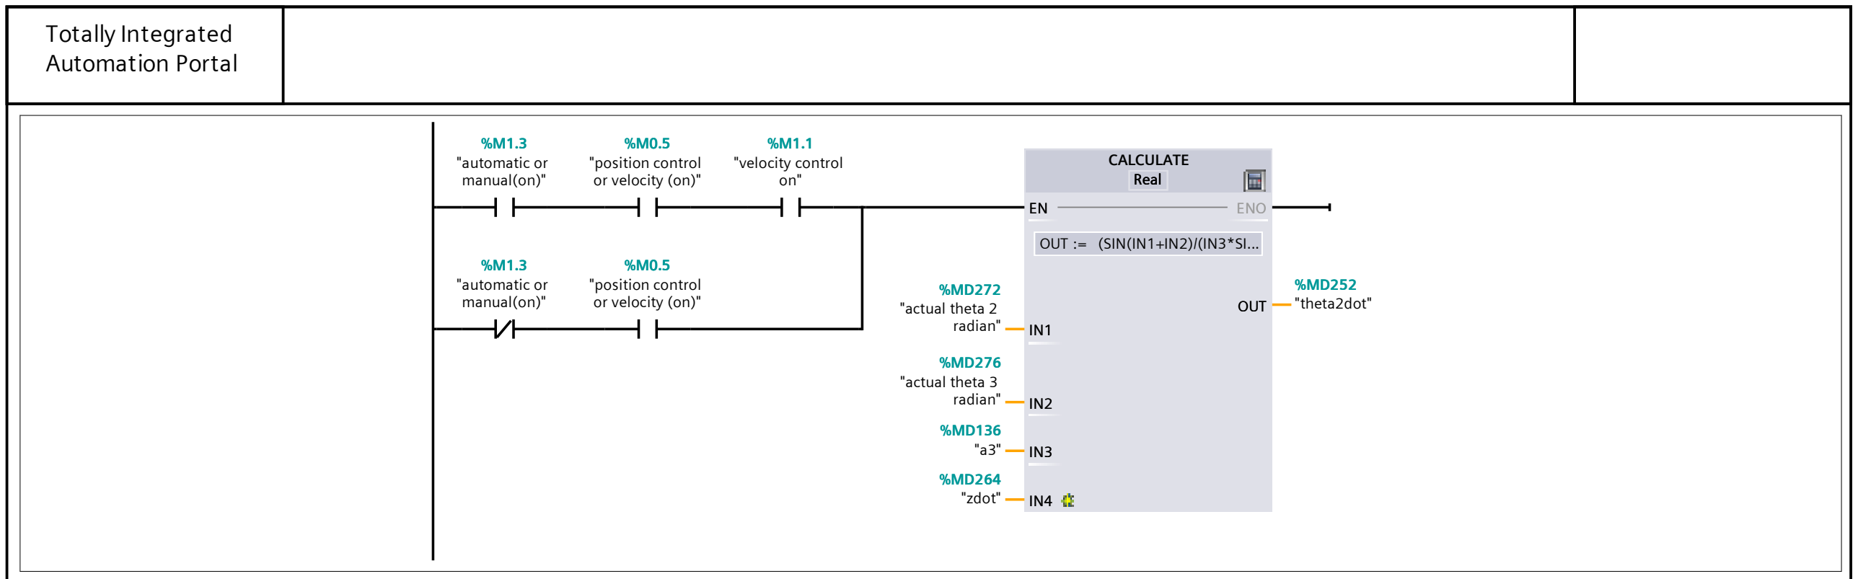
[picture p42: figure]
Automation Portal; OUT := (SIN(IN1+IN2)/(IN3*SI...; CALCULATE Real; "automatic or manual(on)"; "position control or velocity (on)"; "velocity control on"; "actual theta 2 radian"; "actual theta 3 radian"; "zdot"; "theta2dot"; ENO; OUT; Real EN; Real

# Network 7:

OUT := (IN6-IN4*SIN(IN1+IN2...

CALCULATE
Real

"automatic or
manual(on)"

%M1.3
"position control
or velocity (on)"

%M0.5
"velocity control
on"

%M1.1

"actual theta 2
radian"

%MD272

"actual theta 3
radian"

%MD276

"a3"

%MD136

"a4"

%MD140

"zdot"

%MD264

0.0

"theta3dot"

%MD256

OUT := (IN6-IN4*SIN(IN1+IN2...

"automatic or
manual(on)"

%M1.3
"position control
or velocity (on)"

%M0.5

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
Real EN

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
Real

## Automation Portal

# Network 8:

MOVE; "automatic or manual(on)"; "position control or velocity (on)"; "theta2dot"; "velocity control on"; ENO; OUT1

# Network 9:

MOVE; "automatic or manual(on)"; "position control or velocity (on)"; "theta3dot"; "velocity control on"; ENO; OUT1

# Network 10:

Automation Portal | ADD

Auto (Real)

"theta2dot"

%MD252

"theta3dot"

%MD256

"actuator3dot"

%MD268

EN

IN1

IN2

ENO

OUT

Auto (Real) EN

IN1

IN2

ENO

OUT

Auto (Real)

Network 11: | MUL Auto (Real)

"theta2dot"

%MD252

57.29578

"theta2dot
degree"

%MD280

EN

IN1
IN2

ENO

OUT

Auto (Real) EN

IN1
IN2

ENO

OUT

Auto (Real)

Network 12: | MUL Auto (Real)

"actuator3dot"

%MD268

57.29578

"actuator3dot
degree"

%MD284

EN

IN1
IN2

ENO

OUT

Auto (Real) EN

IN1
IN2

ENO

OUT

Auto (Real)

# Network 13:

## Automation Portal

ABS
Real

"theta2dot
degree"

%MD280
"theta2dot_
degree_absolute"

%MD456

EN

IN

ENO

OUT

Real

# Network 14:

ABS
Real

"actuator3dot
degree"

%MD284
"actuator3dot_
degree_absolute"

%MD460

EN

IN

ENO

OUT

Real

# Network 15:

Real >=

"theta2dot
degree"

%MD280

0.0

"move jog for
axis2"

%M9.6

# Network 16:

## Automation Portal

Real >=

"actuator3dot
degree"

%MD284

0.0

"move jog for
axis3"

%M10.0

# Network 17:

MC_MoveJog; "MC_MoveJog_ DB"; "Axis_2"; "theta2dot_ degree_absolute"; true; false false; false false 16#0 16#0; "on mode"; "move jog on"; "already home"; "MC_Move Absolute_DB_1". Busy; "MC_Move Absolute_DB_2".; Busy; "motion valid"; "halt on"; "move jog for; axis2"; "automatic or manual(on)"; "velocity control on"; Axis; JogForward; JogBackward; Velocity Position Controlled; ENO InVelocity Busy Command Aborted; Error ErrorID; ErrorInfo

## Automation Portal

# Network 18:

MC_MoveJog; "MC_MoveJog_ DB_1"; "Axis_3"; "actuator3dot_ degree_absolute"; true; false false; false false 16#0 16#0; "on mode"; "move jog on"; "already home"; "MC_Move Absolute_DB_2". Busy; "MC_Move Absolute_DB_1".; Busy; "motion valid"; "halt on"; "move jog for; axis3"; "automatic or manual(on)"; "velocity control on"; Axis; JogForward; JogBackward; Velocity Position Controlled; ENO InVelocity Busy Command Aborted; Error ErrorID; ErrorInfo

# Network 19:

Automation Portal; "position control or velocity (on)"; "execute; absolute position"; "move jog on"

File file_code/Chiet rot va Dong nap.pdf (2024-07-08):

## Totally Integrated Automation Portal

# fix_plc / PLC_1 [CPU 1214C DC/DC/DC] / Program blocks

# Chiet rot va Dong nap [FC12]

## Chiet rot va Dong nap Properties General

Name | Chiet rot va Dong nap | Number | 12 | Type | FC | Language | LAD
Numbering | Automatic

## Information

Title | | Author | Comment | Family
Version | 0.1 | User-defined ID

## Chiet rot va Dong nap

Name | Data type | Default value | Comment

## Input Output InOut Temp Constant Return

Chiet rot va Dong nap | Void

# Network 1:

"sensor entrance"; "sensor out"; "entrance on"

## Automation Portal

# Network 2:

"on mode"

%M1.6
"conveyor out"

%Q8.3

# Network 3:

"on mode"; "conveyor out; not"; "conveyor in"

# Network 4:

"state5"

%M2.3 | "conveyor out not"

%M9.4

"state6"

%M2.4

"state7"

%M2.6

# Network 5:

## Automation Portal

TON
Time

MOVE

"entrance on"

%M12.1

"timer input"

%DB58

T#15s | T#0ms

180.0 "MC_Move
Relative_DB_3".
Distance

IN

PT | Q ET

# Time EN

IN

ENO

OUT1

IN

PT | Q ET

# Time EN

IN

ENO

OUT1

# Network 6:

Time >; Time <=; "timer input".ET; "pump"; "water valve"

# Network 7: Start command

Time >; "timer input".ET; "sensor cylinder"; "MC_Move Relative_DB_3".; Busy; "excecute disk"

## Automation Portal

Network 8: | R

"MC_Move
Relative_DB_3". Done | "excecute disk" %M12.2

# Network 9:

Time >

# Time <= MOVE

"sensor cylinder"

%I8.1 | "timer input".ET

T#11s

"timer input".ET

T#13s

"cylinder"

%Q8.0

90.0 "MC_Move
Relative_DB_3".

Distance EN
IN

ENO

OUT1

Network 10: Start command | N | S

"cylinder"; "Tag_1"; "MC_Move Relative_DB_3".; Busy; "sensor out"; "excecute disk"

## Automation Portal

# Network 11:

MC_MoveRelative

"MC_Move
Relative_DB_3"

%DB49

"Axis_4"

%DB42

"MC_Move Relative_DB_3". Distance 30.0

false
false

false
false
16#0
16#0

"excecute disk"

%M12.2

EN

# Axis Execute Distance

Velocity

ENO
Done Busy

Command
Aborted
Error ErrorID

ErrorInfo

EN

# Axis Execute Distance

Velocity

ENO
Done Busy

Command
Aborted
Error ErrorID

ErrorInfo

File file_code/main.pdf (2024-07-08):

## Totally Integrated Automation Portal

# fix_plc / PLC_1 [CPU 1214C DC/DC/DC] / Program blocks

# Main [OB1]

## Main Properties General

Name | Main | Number | 1 | Type | OB | Language | LAD
Numbering | Automatic

## Information

Title | "Main Program Sweep (Cy‐ cle)" | Author | Comment | Family
Version | 0.1 | User-defined ID

## Main

Name | Data type | Default value | Comment

## Input

Initial_Call | Bool | | Initial call of this OB
Remanence | Bool | | =True, if remanent data are available

## Temp Constant

Network 1:; "hmi ready"; "on mode"; "Red Led"; "Yellow Led"

## Automation Portal

# Network 2:

"the rest of the system"

%FC4

EN | ENO

# Network 3:

CTRL_HSC; "CTRL_HSC_0_DB"; "Local~HSC_1"; "DOC_HSC".DIR "DOC_HSC".CV "DOC_HSC".RV; "DOC_HSC". PERIOD; "DOC_HSC".NEW_ DIR; "DOC_HSC".NEW_ CV; "DOC_HSC".NEW_ RV; "DOC_HSC".NEW_ PERIOD; False 16#0; HSC DIR CV; PERIOD; NEW_DIR; NEW_CV; NEW_RV; NEW_PERIOD; ENO BUSY; STATUS EN; ENO BUSY STATUS

# Network 4:

## Automation Portal

MOVE

"hsc counter"

%ID1000

"DOC_HSC".XUNG

EN

IN

ENO
OUT1

# Network 5:

NORM_X
Int to Real

SCALE_X
Real to Real MUL Auto (Real)

0

"Tag_4"

%IW66

27648

"Tag_5"

%MD800 | 0.0
| "Tag_5"

%MD800

5000.0

"Temp mass"

%MD804

"Temp mass"

%MD804

2.0

"KL bottle in box"

%MD808

ENMIN

VALUE MAX

ENO

OUT

Int to Real | ENMIN

VALUE MAX

ENO

OUT

Real to Real EN

IN1
IN2

ENO

OUT

# Auto (Real) ENMIN

VALUE MAX

ENO

OUT

Int to Real | ENMIN

VALUE MAX

ENO

OUT

Real to Real EN

IN1
IN2

ENO

OUT

Auto (Real)

# Network 6:

"Set Home Position for Robot"

%FC5

EN | ENO

# Network 7:

## Automation Portal

"Power_On and MC_Home"

%FC9

EN | ENO

# Network 8:

"Calculate Robot"

%FC8

EN | ENO

# Network 9: SET HOME ROBOT

"home"; "read home; done1"; "read encoder done2"; "read encoder done3"; "read home mode1"; "Home button"; "read home mode2"; "read home mode3"; "home disk done"; "set home disk"

# Network 10: KHOI DONG HE THONG

Automation Portal; "start"; "stop"; "automatic or; manual(on)"; "stop button"; "already home"; "on mode"; "start button"; "san pham loi"; "Green Led"

# Network 11:

"ABSB0_1"

%I0.0
"ABSB0_2"

%I0.3
"ABSB0_3"

%I0.6
"in position"

%M9.3

# Network 12:

"Motion Control"

%FC10

EN | ENO

# Network 13:

## Automation Portal

"Change Position of Robot"

%FC6

EN | ENO

# Network 14:

"Change Velocity of Robot"

%FC7

EN | ENO

# Network 15:

## Automation Portal

Network 15: (1.1 / 3.1) | N

IN_RANGE; Real; Int ==; ADD; Auto (Int); "on mode"; "state12"; "ons1"; "bottle position order"; MIN; VAL MAX; ENO; OUT; Real MIN; VAL Real; 2.1 ( Page1 - 8)

"chai co nap"

Auto (Int) MIN

"KL bottle in box"

"KL bottle in box" %MD808

## Automation Portal

## Network 15: (2.1 / 3.1)

1.1 ( Page1 - 7); IN_RANGE; Real; Int ==; "bottle position order"; MAX MIN; VAL MAX; Real MIN; 3.1 ( Page1 - 9)

"KL bottle in box"

## Automation Portal

## Network 15: (3.1 / 3.1)

IN_RANGE; Real; Int ==; "bottle position order"; VAL MAX

2.1 ( Page1 - 8)
Real VAL MAX MIN

VAL MAX MIN

"KL bottle in box"

"box about to full"

"box is full"

## Automation Portal

# Network 16:

MOVE; "change box"; "box is full"; "bottle position order"; "change box button"; "san pham loi"; "Yellow Led"; "box about to full"; ENO; OUT1

# Network 17:

Automation Portal; R MOVE; "start"; "start ons"; "box about to full"; "box is full"; "bottle position order"; ENO; OUT1

# Network 18:

MOVE

"array position". "bottle position

x"["bottle
position order"]

"bottle position x"

%MD362

EN

IN

ENO

OUT1

# Network 19:

MOVE

"array position". "bottle position

y"["bottle
position order"]

"bottle position y"

%MD366

EN

IN

ENO

OUT1

## Automation Portal

# Network 20:

"state5"; "automatic or; manual(on)"; "pneumatic valve"; "state6"; "state7"; "state8"; "state9"; "valve manual"; "on mode"

# Network 21:

Automation Portal; MOVE; "state1"; "state2"; "state3"; "state4"; "state5"; "state6"; "state7"; "state8"; "state9"; "state10"; "state11"; "state12"; "Current state"; ENO; OUT1

# Network 22:

"state1" | MOVE

%M1.7

1
"Current state"

%MW340

EN
IN

ENO

OUT1

# Network 23:

"state2" | MOVE

%M2.0

2
"Current state"

%MW340

EN
IN

ENO

OUT1

# Network 24:

## Automation Portal

"state3" | MOVE

%M2.1

3
"Current state"

%MW340

EN
IN

ENO

OUT1

# Network 25:

"state4" | MOVE

%M2.2

4
"Current state"

%MW340

EN
IN

ENO

OUT1

# Network 26:

"state5" | MOVE

%M2.3

5
"Current state"

%MW340

EN
IN

ENO

OUT1

# Network 27:

"state6" | MOVE

%M2.4

6
"Current state"

%MW340

EN
IN

ENO

OUT1

## Automation Portal

# Network 28:

"state7" | MOVE

%M2.6

7
"Current state"

%MW340

EN
IN

ENO

OUT1

# Network 29:

"state8" | MOVE

%M2.7

8
"Current state"

%MW340

EN
IN

ENO

OUT1

# Network 30:

"state9" | MOVE

%M3.0

9
"Current state"

%MW340

EN
IN

ENO

OUT1

# Network 31:

## Automation Portal

"state10" | MOVE

%M3.4

10
"Current state"

%MW340

EN
IN

ENO

OUT1

# Network 32:

"state11" | MOVE

%M3.5

11
"Current state"

%MW340

EN
IN

ENO

OUT1

# Network 33:

"state12" | MOVE

%M3.7

12
"Current state"

%MW340

EN
IN

ENO

OUT1

# Network 34:

Automation Portal | Int>

"bottle position
order"

%MW342

0

"bottle0"

%M4.3

# Network 35:

Int>

"bottle position
order"

%MW342

1

"bottle1"

%M4.4

# Network 36:

Int>

"bottle position
order"

%MW342

2

"bottle2"

%M4.5

# Network 37:

Automation Portal | Int>

"bottle position
order"

%MW342

3

"bottle3"

%M4.6

# Network 38:

Int>

"bottle position
order"

%MW342

4

"bottle4"

%M4.7

# Network 39:

Int>

"bottle position
order"

%MW342

5

"bottle5"

%M5.0

# Network 40:

Automation Portal | Int>

"bottle position
order"

%MW342

6

"bottle6"

%M5.1

# Network 41:

Int>

"bottle position
order"

%MW342

7

"bottle7"

%M5.2

# Network 42:

"box is full"

%M4.0
"bottle8"

%M5.3

# Network 43:

## Automation Portal

MOVE

"automatic or
manual(on)"

%M1.3
"position control
or velocity (on)"

%M0.5

"px manual"

%MD304
"px"

%MD100

EN

IN

ENO

OUT1

# Network 44:

MOVE

"automatic or
manual(on)"

%M1.3
"position control
or velocity (on)"

%M0.5

"py manual"

%MD308
"py"

%MD104

EN

IN

ENO

OUT1

# Network 45:

MOVE

"automatic or
manual(on)"

%M1.3
"position control
or velocity (on)"

%M0.5

"pz manual"

%MD312
"pz"

%MD108

EN

IN

ENO

OUT1

# Network 46:

## Automation Portal

MOVE

"automatic or
manual(on)"

%M1.3
"position control
or velocity (on)"

%M0.5

"zdot manual"

%MD370
"zdot"

%MD264

EN

IN

ENO

OUT1

# Network 47:

"start velocity control"; "stop velocity control"; "automatic or manual(on)"; "position control or velocity (on)"; "velocity control on"

# Network 48:

Real <=; Real >=; "theta1degree"; "theta2degree"; "actuator3degree; "motion valid"

# Network 49:

## Automation Portal

## Network 49: (1.1 / 2.1) ADD

Auto (Real); SUB Auto (Real); OUT_RANGE Real; ADD Auto (Real); OUT_RANGE Real ADD; "actual px"; "automatic or manual(on)"; "already home"; "execute absolute position"; "position control or velocity (on)"; "on mode"; "actual py"; "pz lower range"; "actual pz"; "pz upper range"; ENO; OUT; MIN; VAL MAX; Real EN; Real; 2.1 ( Page1 - 23)

"px upper range"

"px lower ranger"

"py upper range"

"py lower ranger"

"pz upper range"

"pz lower range"

## Automation Portal

## Network 49: (2.1 / 2.1)

1.1 ( Page1 - 22)

## Automation Portal

Network 50:; "MC_Move Absolute_DB". Done; "MC_Move Absolute_DB_1". Done; "MC_Move Absolute_DB_2". Done; "automatic or manual(on)"; "execute; absolute position"

# Network 51:

MOVE

"automatic or
manual(on)"

%M1.3
"inverse or
forward"

%M0.3

"theta1forward"

%MD236
"theta1degree"

%MD208

EN

IN

ENO

OUT1

# Network 52:

MOVE

"automatic or
manual(on)"

%M1.3
"inverse or
forward"

%M0.3

"theta2forward"

%MD240
"theta2degree"

%MD212

EN

IN

ENO

OUT1

# Network 53:

## Automation Portal

MOVE

"automatic or
manual(on)"

%M1.3
"inverse or
forward"

%M0.3

"theta3forward"

%MD244
"theta3degree"

%MD216

EN

IN

ENO

OUT1

# Network 54:

"already home"; "on mode"; "automatic or; manual(on)"; "halt on"

# Network 55:

MC_ReadParam
Real

"MC_ReadParam_
DB"

%DB14

1
"Axis_1".Actual
Position

"actual theta1
degree"

%MD224

false

false EN
Enable

Parameter Value

ENO
Valid

Error Real EN

Enable

Parameter Value

ENO
Valid

Error Real

# Network 56:

## Automation Portal

MC_ReadParam
Real

"MC_ReadParam_
DB_1"

%DB15

1
"Axis_2".Actual
Position

"actual theta 2
degree"

%MD228

false

false EN
Enable

Parameter Value

ENO
Valid

Error Real EN

Enable

Parameter Value

ENO
Valid

Error Real

# Network 57:

MC_ReadParam
Real

"MC_ReadParam_
DB_2"

%DB16

1
"Axis_3".Actual
Position

"actual actuator

### 3 degree"

%MD232

false

false EN
Enable

Parameter Value

ENO
Valid

Error Real EN

Enable

Parameter Value

ENO
Valid

Error Real

# Network 58:

## Automation Portal

MC_ReadParam
Real

"MC_ReadParam_
DB_3"

%DB31

false
"Axis_2".Actual
Velocity

"actual theta 2
velocity"

%MD374

false

false EN
Enable

Parameter Value

ENO
Valid

Error Real EN

Enable

Parameter Value

ENO
Valid

Error Real

# Network 59:

MC_ReadParam
Real

"MC_ReadParam_
DB_4"

%DB32

false
"Axis_3".Actual
Velocity

"actual actuator

### 3 velocity"

%MD378

false

false EN
Enable

Parameter Value

ENO
Valid

Error Real EN

Enable

Parameter Value

ENO
Valid

Error Real

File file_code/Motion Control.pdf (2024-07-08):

## Totally Integrated Automation Portal

# fix_plc / PLC_1 [CPU 1214C DC/DC/DC] / Program blocks

# Motion Control [FC10]

## Motion Control Properties General

Name | Motion Control | Number | 10 | Type | FC | Language | LAD
Numbering | Automatic

## Information

Title | | Author | Comment | Family
Version | 0.1 | User-defined ID

## Motion Control

Name | Data type | Default value | Comment

## Input Output InOut Temp Constant Return

Motion Control | Void

# Network 1:

Automation Portal; MC_MoveAbsolute; "MC_Move Absolute_DB"; "Axis_1"; "theta1degree"; false false; false false 16#0 16#0; "execute absolute position"; "motion valid"; "automatic or; manual(on)"; "halt on"; "already home"; "automatic or manual(on)"; "execute absolute manual"; "position control; or velocity (on)"; EN Axis Execute; Position Velocity Direction; ENO Done Busy; Command Aborted; Error ErrorID; ErrorInfo

# Network 2:

MC_MoveAbsolute; "MC_Move Absolute_DB_1"; "Axis_2"; "theta2degree"; false false; false false 16#0 16#0; "execute absolute position"; "motion valid"; "automatic or; manual(on)"; "MC_MoveJog_; DB".Busy; "halt on"; DB_1".Busy; "already home"; "automatic or manual(on)"; "execute absolute manual"; "position control; or velocity (on)"; EN Axis Execute; Position Velocity Direction; ENO Done Busy; Command Aborted; Error ErrorID; ErrorInfo

## Automation Portal

# Network 3:

MC_MoveAbsolute; "MC_Move Absolute_DB_2"; "Axis_3"; "actuator3degree; false false; false false 16#0 16#0; "execute absolute position"; "motion valid"; "automatic or; manual(on)"; "MC_MoveJog_; DB".Busy; "halt on"; DB_1".Busy; "already home"; "automatic or manual(on)"; "execute absolute manual"; "position control; or velocity (on)"; EN Axis Execute; Position Velocity Direction; ENO Done Busy; Command Aborted; Error ErrorID; ErrorInfo

# Network 4: Dừng chuyển động của trục

MC_Halt; "MC_Halt_DB"; "Axis_1"; false false; "already home"; "on mode"; "automatic or; manual(on)"; Axis Execute; ENO; Done Error EN; Done Error

## Automation Portal

# Network 5:

MC_Halt; "MC_Halt_DB_1"; "Axis_2"; false; "already home"; "on mode"; "automatic or; manual(on)"; Axis Execute; ENO; Done Error EN; Done Error Network 6:
MC_Halt; "MC_Halt_DB_2"; "Axis_3"; false false; "already home"; "on mode"; "automatic or; manual(on)"; Axis Execute; ENO; Done Error EN; Done Error

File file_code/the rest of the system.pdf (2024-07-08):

## Totally Integrated Automation Portal

# fix_plc / PLC_1 [CPU 1214C DC/DC/DC] / Program blocks

# the rest of the system [FC4]

## the rest of the system Properties General

Name | the rest of the system | Number | 4 | Type | FC | Language | LAD
Numbering | Automatic

## Information

Title | | Author | Comment | Family
Version | 0.1 | User-defined ID

## the rest of the system

Name | Data type | Default value | Comment

## Input Output InOut Temp Constant Return

the rest of the system | Void

# Network 1:

"the rest"."test; mode (on)"; "sensor entrance"; "the rest".; "the rest"."test mode (on)"; "the rest". "sensor entrance test"

## Automation Portal

# Network 2:

"the rest"."test; mode (on)"; "sensor cylinder"; "the rest".; "the rest"."test mode (on)"; "the rest". "sensor cylinder test"

# Network 3:

"the rest"."test; mode (on)"; "sensor out"; "the rest".; "sensor output"; "the rest"."test mode (on)"; "the rest". "sensor output test"

# Network 4:

Automation Portal; "the rest"."start the rest"; "the rest"."stop; the rest"; "Red Led"; "already home"; "the rest". "onmode the rest"; "on mode"

# Network 5:

"the rest". "onmode the; rest"; "not conveyor in"; "conveyor in"

# Network 6:

Automation Portal; CTUD Int P; Int>; "the rest". "sensor entrance"; "the rest". "entrance free"; "MC_Move Relative_DB_3". Busy; "number of bottle"; false4; false 0; "the rest"."output free"; "the rest"."output free ons"; "number of bottle".CV; "the rest". "manual reset the rest"; "the rest". "onmode the rest"; QUQD; Int CU; Int

# Network 7:

"the rest".
"entrance free"

"the rest".
"cylinder free"

"the rest"."output
free" | "the rest".free

# Network 8:

Automation Portal; Int>; "the rest".free; "number of bottle".CV; "the rest". "execute relative"; "delay mam xoay".Q; "the rest". "sensor output"; "MC_Move Relative_DB_3". Busy; "het chai trong dia"; "box is full"; "the rest".; "execute relative"

# Network 9:

TON
Time

"MC_Move
Relative_DB_3".
Busy

"delay mam xoay"

%DB53

T#5s | T#0ms

IN

PT | Q ET

Time

Network 10: | R

"MC_Move
Relative_DB_3". Done
"the rest".
"execute relative"

# Network 11:

## Automation Portal

TONR
"conveyor in" | Time
%Q8.2 | "the rest"."bottle at output" "the rest". "sensor output" "IEC_Timer_0_DB_ 1"

%DB50

T#1s | T#0ms

"MC_Move
Relative_DB_3".
Busy

IN

R

PT | Q ET

Time
IN

R

PT | Q ET

Time

# Network 12:

P_TRIG; "the rest". "sensor output"; "MC_Move Relative_DB_3". Busy; "the rest"."ons for bottle at output"; "the rest"."bottle at output"; CLK

Network 13: | R

"IEC_Timer_0_DB_
1".Q

"the rest"."bottle
at output"

# Network 14:

Automation Portal; "the rest"."bottle at output"; "the rest"."output free"

# Network 15:

P_TRIG; "the rest". "sensor cylinder"; "MC_Move Relative_DB_3". Busy; "the rest". "cylinder free ons"; "the rest". "cylinder free"; CLK

Network 16: | TP

Time

"the rest".
"cylinder free"

"cylinder timer"

%DB51

T#5s | T#0ms

IN

PT | Q ET

Time

# Network 17:

Automation Portal; Time >; Time <; "the rest". "onmode the rest"; "the rest".; "cylinder free"; "cylinder timer".ET; "cylinder"

Network 18: | N | S

"cylinder timer".Q

"the rest".
"cylinder timer
ons"

"the rest".
"cylinder free"

# Network 19:

P_TRIG; "the rest". "sensor entrance"; "MC_Move Relative_DB_3". Busy; "the rest". "sensor entrance ons"; "the rest". "entrance free"; CLK

# Network 20:

Automation Portal | TP

Time

"the rest".
"sensor entrance"

"MC_Move
Relative_DB_3".
Busy

"timer entrance"

%DB25

T#4.5s | T#0ms

IN

PT | Q ET

Time

# Network 21: 1.68L/p

Time >; DInt <; "timer entrance". ET; "DOC_HSC".XUNG; "the rest". "onmode the; rest"; "water valve"; "DOC_HSC".CV; "the rest".; "sensor entrance"; "pump"; "not conveyor in"

# Network 22:

Automation Portal | N | S

"timer entrance".
Q

"the rest"."timer
entrance ons"

"the rest".
"entrance free"

# Network 23:

"state5"

%M2.3 | "conveyor out not"

%M9.4

"state6"

%M2.4

"state7"

%M2.6

# Network 24:

"the rest". "onmode the rest"; "conveyor out not"; "conveyor out"

# Network 25:

Automation Portal; "sensor out"; "Tag_6"; "sensor entrance"; "sensor cylinder"; "het chai trong; dia"

# Network 26:

MC_MoveRelative

"MC_Move
Relative_DB_3"

%DB49

"Axis_4"

%DB42

90.0
30.0

false
false
"the rest".
"execute relative" | EN
| Axis Execute Distance

Velocity

ENO

Done Error EN

Axis Execute Distance

Velocity

ENO

# Done Error Network 27:

## Automation Portal

MC_ReadParam
Real

"MC_ReadParam_
DB_5"

%DB55

1
"Axis_4".Actual
Position

"actual theta4"

%MD452

false

false EN
Enable

Parameter Value

ENO
Valid

Error Real EN

Enable

Parameter Value

ENO
Valid

Error Real

# Network 28:

MC_MoveJog

"MC_MoveJog_
DB_2"

%DB52

"Axis_4"

%DB42

false 15.0

false
false

"set home disk"

%M14.0 | "Sensor Home Disk"

%I8.7

EN

Axis

JogForward
JogBackward
Velocity

ENO

InVelocity Error EN

Axis

JogForward
JogBackward
Velocity

ENO
InVelocity Error Network 29:

Automation Portal; "Sensor Home Disk"; "set home disk"; "home disk done"

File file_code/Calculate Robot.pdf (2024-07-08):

## Totally Integrated Automation Portal

# fix_plc / PLC_1 [CPU 1214C DC/DC/DC] / Program blocks

# Calculate Robot [FC8]

## Calculate Robot Properties General

Name | Calculate Robot | Number | 8 | Type | FC | Language | LAD
Numbering | Automatic

## Information

Title | | Author | Comment | Family
Version | 0.1 | User-defined ID

## Calculate Robot

Name | Data type | Default value | Comment

## Input Output InOut Temp Constant Return

Calculate Robot | Void

# Network 1:

## Automation Portal

Real > | OUT := ATAN(IN2/IN1)+ASIN(I... CALCULATE
Real "px"

%MD100

0.0

"px"

%MD100

"py"

%MD104

"a6"

%MD148

"theta1"

%MD112

OUT := ATAN(IN2/IN1)+ASIN(I... EN

IN1

IN2

IN3

ENO

OUT

Real EN

IN1

IN2

IN3

ENO

OUT

Real

# Network 2:

Real < | OUT := ATAN(IN2/IN1)+ASIN(I... CALCULATE
Real "px"

%MD100

0.0

"px"

%MD100

"py"

%MD104

"a6"

%MD148

3.14159

"theta1"

%MD112

OUT := ATAN(IN2/IN1)+ASIN(I... EN

IN1

IN2

IN3
IN4

ENO

OUT

Real EN

IN1

IN2

IN3
IN4

ENO

OUT

Real

# Network 3:

## Automation Portal

Real == | OUT := ASIN(IN3/SQRT(SQR(I... CALCULATE
Real "px"

%MD100

0.0

"px"

%MD100

"py"

%MD104

"a6"

%MD148

1.5708

"theta1"

%MD112

OUT := ASIN(IN3/SQRT(SQR(I... EN

IN1

IN2

IN3
IN4

ENO

OUT

Real EN

IN1

IN2

IN3
IN4

ENO

OUT

Real

# Network 4:

OUT := IN1*COS(IN3)+IN2*SI...

CALCULATE
Real

"px"

%MD100

"py"

%MD104

"theta1"

%MD112

"a2"

%MD132

"a5"

%MD144

"K1"

%MD160

OUT := IN1*COS(IN3)+IN2*SI... EN

IN1

IN2

IN3

IN4

IN5

ENO

OUT

Real EN

IN1

IN2

IN3

IN4

IN5

ENO

OUT

Real

# Network 5:

## Automation Portal

OUT := IN1-IN2

CALCULATE
Real

"pz"

%MD108

"d1"

%MD128

"K2"

%MD164

OUT := IN1-IN2

EN

IN1

IN2

ENO

OUT

Real EN

IN1

IN2

ENO

OUT

Real

# Network 6:

OUT := IN5-ACOS((IN1*IN1+I...

CALCULATE
Real

"K1"

%MD160

"K2"

%MD164

"a3"

%MD136

"a4"

%MD140

0.0
2.0

"theta3"

%MD120

OUT := IN5-ACOS((IN1*IN1+I... EN

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
Real EN

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
Real

# Network 7:

## Automation Portal

OUT := (IN2*(IN4*COS(IN6)+...

CALCULATE
Real

"K1"

%MD160

"K2"

%MD164

"a3"

%MD136

"a4"

%MD140

"a2"

%MD132

"theta3"

%MD120

"theta2y"

%MD152

OUT := (IN2*(IN4*COS(IN6)+... EN

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
Real EN

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
Real

# Network 8:

OUT := (IN1+IN2*SIN(IN3)*IN...

CALCULATE
Real

"K1"

%MD160

"a4"

%MD140

"theta3"

%MD120

"theta2y"

%MD152

"a3"

%MD136

"theta2x"

%MD156

OUT := (IN1+IN2*SIN(IN3)*IN... EN

IN1

IN2

IN3

IN4

IN5

ENO

OUT

Real EN

IN1

IN2

IN3

IN4

IN5

ENO

OUT

Real

# Network 9:

## Automation Portal

Real > | OUT := ATAN(IN2/IN1) CALCULATE
Real "theta2x"

%MD156

0.0

"theta2x"

%MD156

"theta2y"

%MD152

"theta2"

%MD116

OUT := ATAN(IN2/IN1) EN

IN1

IN2

ENO

OUT

Real EN

IN1

IN2

ENO

OUT

Real

# Network 10:

Real < | OUT := ATAN(IN2/IN1)+IN3 CALCULATE
Real "theta2x"

%MD156

0.0

"theta2x"

%MD156

"theta2y"

%MD152

3.14159

"theta2"

%MD116

OUT := ATAN(IN2/IN1)+IN3

EN

IN1

IN2
IN3

ENO

OUT

Real EN

IN1

IN2
IN3

ENO

OUT

Real

# Network 11:

Real == | MOVE "theta2x"

%MD156

0.0 1.5708
"theta2"

%MD116

EN
IN

ENO

OUT1

## Automation Portal

Network 12: | MUL Real

"inverse or
forward"

%M0.3

"theta1"

%MD112

57.29578

"theta1degree"

%MD208

"automatic or
manual(on)"

%M1.3

EN

IN1
IN2

ENO

OUT

Real EN

IN1
IN2

ENO

OUT

Real

Network 13: | MUL Auto (Real)

"inverse or
forward"

%M0.3

"theta2"

%MD116

57.29578

"theta2degree"

%MD212

"automatic or
manual(on)"

%M1.3

EN

IN1
IN2

ENO

OUT

Auto (Real) EN

IN1
IN2

ENO

OUT

Auto (Real)

# Network 14:

Automation Portal | MUL Auto (Real)

"inverse or
forward"

%M0.3

"theta3"

%MD120

57.29578

"theta3degree"

%MD216

"automatic or
manual(on)"

%M1.3

EN

IN1
IN2

ENO

OUT

Auto (Real) EN

IN1
IN2

ENO

OUT

Auto (Real)

Network 15: | ADD

Real

"theta2degree"

%MD212

"theta3degree"

%MD216

150.0

"actuator3degree

"%MD220

EN

IN1

IN2
IN3

ENO

OUT

Real EN

IN1

IN2
IN3

ENO

OUT

Real

# Network 16:

## Automation Portal

OUT := IN1-IN2-IN3

CALCULATE
Real

"actual actuator

### 3 degree"

%MD232

"actual theta 2
degree"

%MD228

150.0

"actual theta3
degree"

%MD248

OUT := IN1-IN2-IN3

EN

IN1

IN2
IN3

ENO

OUT

Real EN

IN1

IN2
IN3

ENO

OUT

Real

Network 17: | DIV

Auto (Real)

"actual theta1
degree"

%MD224

57.29578

"actual theta 1
radian"

%MD300

EN

IN1
IN2

ENO

OUT

Auto (Real) EN

IN1
IN2

ENO

OUT

Auto (Real)

Network 18: | DIV

Real

"actual theta 2
degree"

%MD228

57.29578

"actual theta 2
radian"

%MD272

EN

IN1
IN2

ENO

OUT

Real EN

IN1
IN2

ENO

OUT

Real

## Automation Portal

Network 19: | DIV

Auto (Real)

"actual theta3
degree"

%MD248

57.29578

"actual theta 3
radian"

%MD276

EN

IN1
IN2

ENO

OUT

Auto (Real) EN

IN1
IN2

ENO

OUT

Auto (Real)

# Network 20:

OUT := COS(IN1)*(IN4+IN6*...

CALCULATE
Real

"actual theta 1
radian"

%MD300

"actual theta 2
radian"

%MD272

"actual theta 3
radian"

%MD276

"a2"

%MD132

"a3"

%MD136

"a4"

%MD140

"a5"

%MD144

"a6"

%MD148

"actual px"

%MD288

OUT := COS(IN1)*(IN4+IN6*... EN

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
Real EN

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
Real

## Automation Portal

# Network 21:

OUT := SIN(IN1)*(IN4+IN6*C...

CALCULATE
Real

"actual theta 1
radian"

%MD300

"actual theta 2
radian"

%MD272

"actual theta 3
radian"

%MD276

"a2"

%MD132

"a3"

%MD136

"a4"

%MD140

"a5"

%MD144

"a6"

%MD148

"actual py"

%MD292

OUT := SIN(IN1)*(IN4+IN6*C... EN

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
Real EN

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
Real

# Network 22:

Automation Portal; OUT := IN7+IN5*SIN(IN2+IN3...; CALCULATE Real; "actual theta 1 radian"; "actual theta 2 radian"; "actual theta 3 radian"; "actual pz"; OUT := IN7+IN5*SIN(IN2+IN3... EN; ENO; OUT; Real EN; Real

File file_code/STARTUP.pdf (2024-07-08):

## Totally Integrated Automation Portal

# fix_plc / PLC_1 [CPU 1214C DC/DC/DC] / Program blocks

# Startup [OB100]

## Startup Properties General

Name | Startup | Number | 100 | Type | OB | Language | LAD
Numbering | Automatic

## Information

Title | "Complete Restart" | Author | Comment | Family
Version | 0.1 | User-defined ID

## Startup

Name | Data type | Default value | Comment

## Input

LostRetentive | Bool | | True if retentive data are lost
LostRTC | Bool | | True if date and time are lost

## Temp Constant

# Network 1:

MOVE

42.0
"a2"

%MD132

EN
IN

ENO

OUT1

# Network 2:

## Automation Portal

MOVE

59.5
"d1"

%MD128

EN
IN

ENO

OUT1

# Network 3:

MOVE

191.0
"a3"

%MD136

EN
IN

ENO

OUT1

# Network 4:

MOVE

191.0
"a4"

%MD140

EN
IN

ENO

OUT1

# Network 5:

MOVE

147.94
"a5"

%MD144

EN
IN

ENO

OUT1

## Automation Portal

# Network 6:

MOVE

13.2
"a6"

%MD148

EN
IN

ENO

OUT1

# Network 7:

MOVE

0.0
"home position 1"

%MD172

EN
IN

ENO

OUT1

# Network 8:

MOVE

0.0
"home position 2"

%MD176

EN
IN

ENO

OUT1

# Network 9:

## Automation Portal

MOVE

90.0
"home position 3"

%MD180

EN
IN

ENO

OUT1

# Network 10:

MOVE | MOVE | MOVE

450.0 "array position".
"bottle position
x"[0]

"array position". "bottle position

x"[0]

"array position".
"bottle position
x"[1]

"array position". "bottle position

x"[0]

"array position".
"bottle position

x"[2] EN
IN

ENO

OUT1

EN

IN

ENO

OUT1

EN

IN

ENO

OUT1

EN
IN

ENO

OUT1

EN

IN

ENO

OUT1

EN

IN

ENO

OUT1

# Network 11:

SUB
Auto (Real) | MOVE | MOVE

"array position". "bottle position

x"[0]
50.0

"array position".
"bottle position
x"[3]

"array position". "bottle position

x"[3]

"array position".
"bottle position
x"[4]

"array position". "bottle position

x"[3]

"array position".
"bottle position

x"[5] EN

IN1
IN2

ENO

OUT

Auto (Real) | EN

IN

ENO

OUT1

EN

IN

ENO

OUT1

EN

IN1
IN2

ENO

OUT

Auto (Real) | EN

IN

ENO

OUT1

EN

IN

ENO

OUT1

# Network 12:

## Automation Portal

SUB
Auto (Real) | MOVE | MOVE

"array position". "bottle position

x"[4]
50.0

"array position".
"bottle position
x"[6]

"array position". "bottle position

x"[6]

"array position".
"bottle position
x"[7]

"array position". "bottle position

x"[6]

"array position".
"bottle position

x"[8] EN

IN1
IN2

ENO

OUT

Auto (Real) | EN

IN

ENO

OUT1

EN

IN

ENO

OUT1

EN

IN1
IN2

ENO

OUT

Auto (Real) | EN

IN

ENO

OUT1

EN

IN

ENO

OUT1

# Network 13:

MOVE | MOVE | MOVE

90.0 "array position".
"bottle position
y"[0]

"array position". "bottle position

y"[0]

"array position".
"bottle position
y"[3]

"array position". "bottle position

y"[0]

"array position".
"bottle position

y"[6] EN
IN

ENO

OUT1

EN

IN

ENO

OUT1

EN

IN

ENO

OUT1

EN
IN

ENO

OUT1

EN

IN

ENO

OUT1

EN

IN

ENO

OUT1

# Network 14:

SUB
Auto (Real) | MOVE | MOVE

"array position". "bottle position

y"[0]
50.0

"array position".
"bottle position
y"[1]

"array position". "bottle position

y"[1]

"array position".
"bottle position
y"[4]

"array position". "bottle position

y"[1]

"array position".
"bottle position

y"[7] EN

IN1
IN2

ENO

OUT

Auto (Real) | EN

IN

ENO

OUT1

EN

IN

ENO

OUT1

EN

IN1
IN2

ENO

OUT

Auto (Real) | EN

IN

ENO

OUT1

EN

IN

ENO

OUT1

# Network 15:

## Automation Portal

SUB
Auto (Real) | MOVE | MOVE

"array position". "bottle position

y"[1]
50.0

"array position".
"bottle position
y"[2]

"array position". "bottle position

y"[2]

"array position".
"bottle position
y"[5]

"array position". "bottle position

y"[2]

"array position".
"bottle position

y"[8] EN

IN1
IN2

ENO

OUT

Auto (Real) | EN

IN

ENO

OUT1

EN

IN

ENO

OUT1

EN

IN1
IN2

ENO

OUT

Auto (Real) | EN

IN

ENO

OUT1

EN

IN

ENO

OUT1

# Network 16:

MOVE

0

"bottle position
order"

%MW342

EN
IN

ENO

OUT1

Network 17: | R

"already home"

%M3.1

Network 18: | R

"execute
absolute
position"

%M0.2

## Automation Portal

Network 19: | R

"position control
or velocity (on)"

%M0.5

Network 20: | S

"read phase
done1"

%M6.5

Network 21: | S

"read phase
done2"

%M7.3

Network 22: | S

"read phase
done3"

%M8.1

## Automation Portal

# Network 23:

S

"the rest".
"cylinder free"

# Network 24:

S

"the rest"."output
free"

# Network 25:

S

"the rest".
"entrance free"

# Network 26:

MOVE

SUB

Auto (Real) | ADD Auto (Real)

72.0
"bottle on
conveyor px"

%MD474
"bottle on
conveyor px"

%MD474

0.01

"bottle on
conveyor px low"

%MD482
"bottle on
conveyor px"

%MD474

0.01

"bottle on
conveyor px high"

%MD486

EN
IN

ENO

OUT1

EN

IN1
IN2

ENO

OUT

Auto (Real) | EN

IN1
IN2

ENO

OUT

Auto (Real) EN

IN

ENO

OUT1

EN

IN1
IN2

ENO

OUT

Auto (Real) | EN

IN1
IN2

ENO

OUT

Auto (Real)

## Automation Portal

# Network 27:

MOVE

SUB

Auto (Real) | ADD Auto (Real)

291.0
"bottle on
conveyor py"

%MD478
"bottle on
conveyor py"

%MD478

0.01

"bottle on
conveyor py low"

%MD490
"bottle on
conveyor py"

%MD478

0.01

"bottle on
conveyor py high"

%MD494

EN
IN

ENO

OUT1

EN

IN1
IN2

ENO

OUT

Auto (Real) | EN

IN1
IN2

ENO

OUT

Auto (Real) EN

IN

ENO

OUT1

EN

IN1
IN2

ENO

OUT

Auto (Real) | EN

IN1
IN2

ENO

OUT

Auto (Real)

# Network 28:

MOVE

SUB

Auto (Real) | ADD Auto (Real)

69.0
"defective bottle
px"

%MD500
"defective bottle
px"

%MD500

0.01

"defective bottle
px low"

%MD508
"defective bottle
px"

%MD500

0.01

"defective bottle
px high"

%MD516

EN
IN

ENO

OUT1

EN

IN1
IN2

ENO

OUT

Auto (Real) | EN

IN1
IN2

ENO

OUT

Auto (Real) EN

IN

ENO

OUT1

EN

IN1
IN2

ENO

OUT

Auto (Real) | EN

IN1
IN2

ENO

OUT

Auto (Real)

# Network 29:

MOVE

SUB

Auto (Real) | ADD Auto (Real)

-321.0
"defective bottle
py"

%MD504
"defective bottle
py"

%MD504

0.01

"defective bottle
py low"

%MD512
"defective bottle
py"

%MD504

0.01

"defective bottle
py high"

%MD520

EN
IN

ENO

OUT1

EN

IN1
IN2

ENO

OUT

Auto (Real) | EN

IN1
IN2

ENO

OUT

Auto (Real) EN

IN

ENO

OUT1

EN

IN1
IN2

ENO

OUT

Auto (Real) | EN

IN1
IN2

ENO

OUT

Auto (Real)

## Automation Portal

# Network 30:

"number of
bottle".R

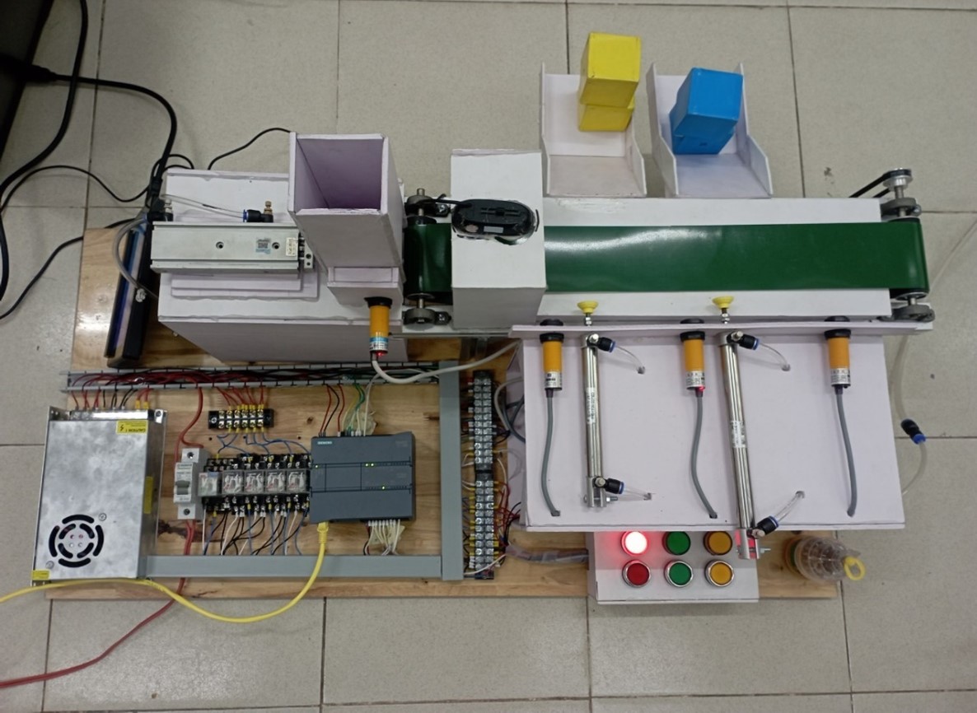
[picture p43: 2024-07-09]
images/hardware.jpg

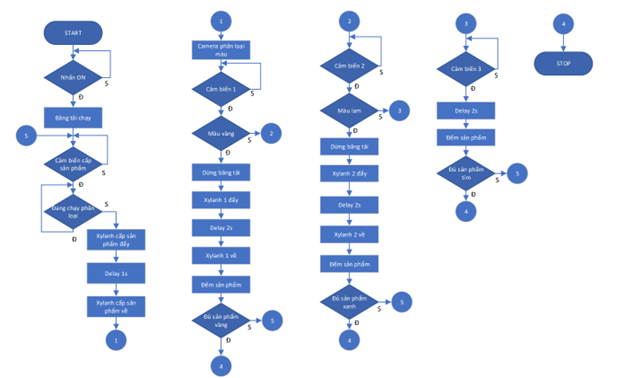
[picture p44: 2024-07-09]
images/diagram.png

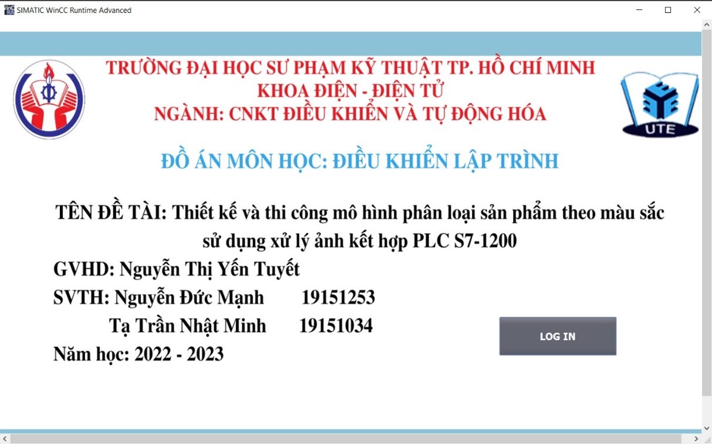
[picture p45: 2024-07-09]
images/scada.jpg

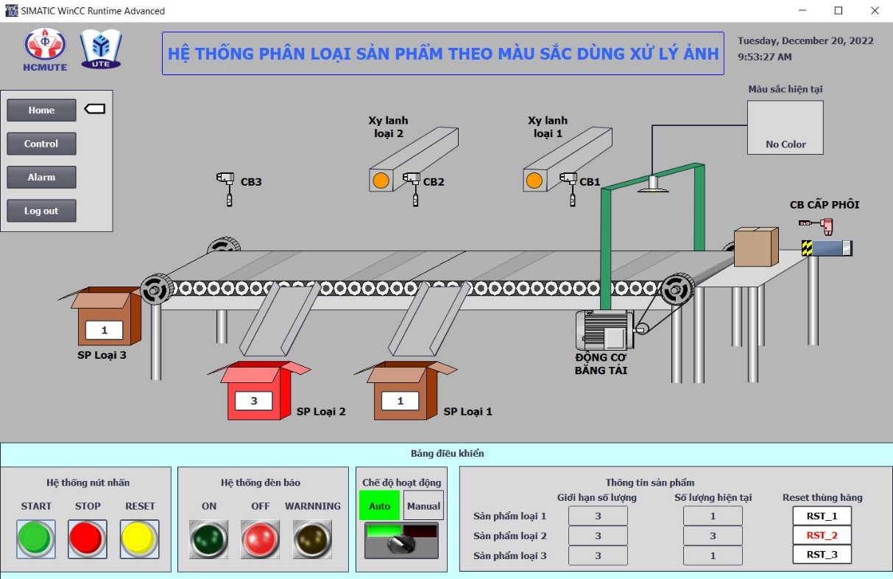
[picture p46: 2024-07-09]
images/xilanh2.jpg

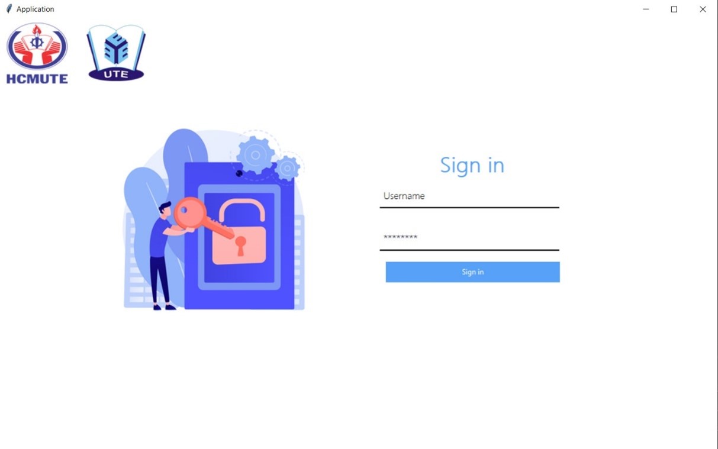
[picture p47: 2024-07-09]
images/gui_start.jpg

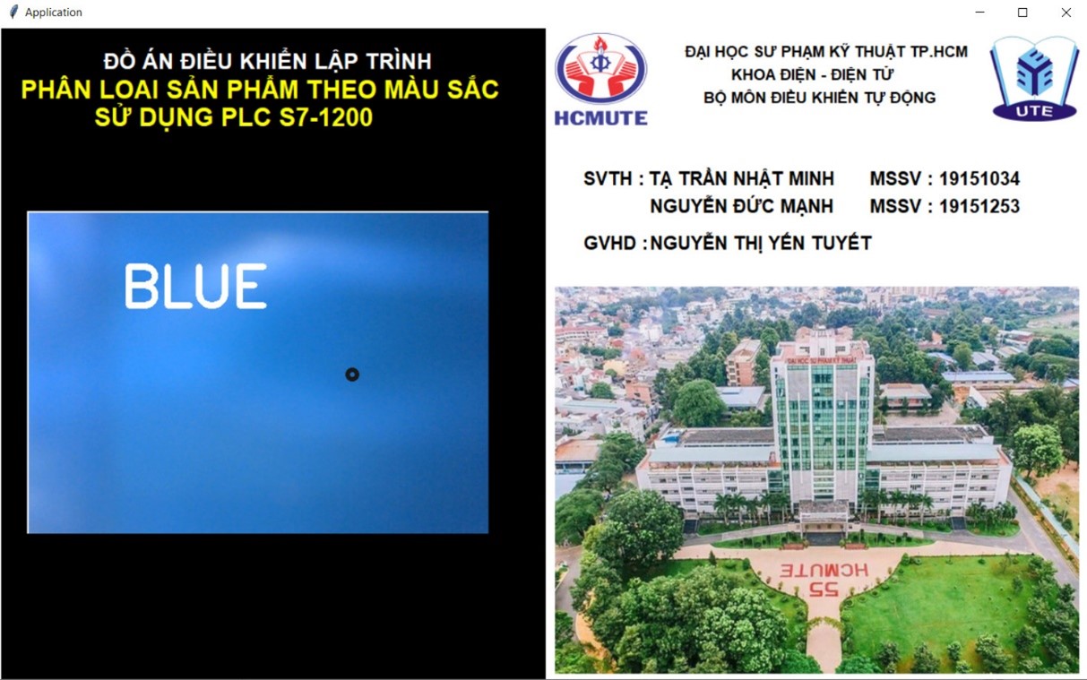
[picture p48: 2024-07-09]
images/blue.jpg

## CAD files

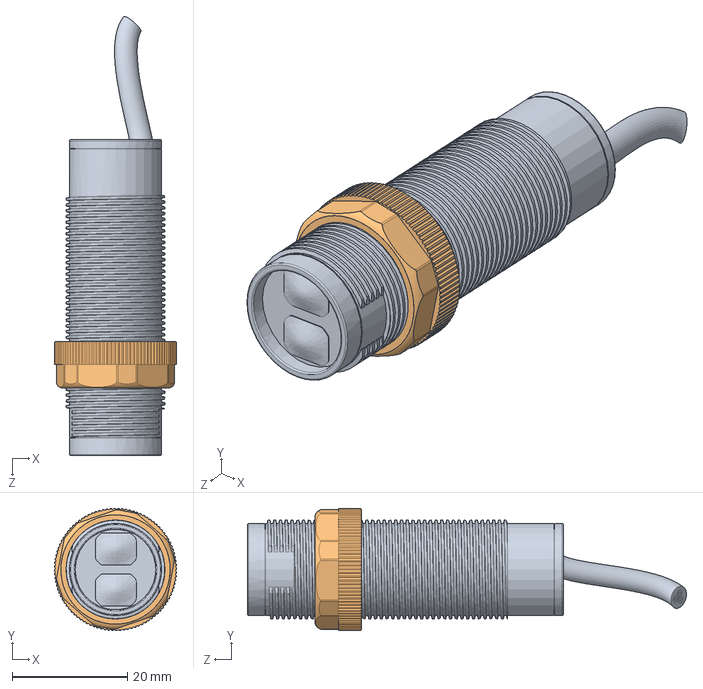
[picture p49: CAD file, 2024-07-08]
solidwork do an tot nghiep/infrared-sensor-2.snapshot.3/IR Sensor.SLDASM
21.2 x 21.2 x 76.2 mm
IR Sensor
Nut

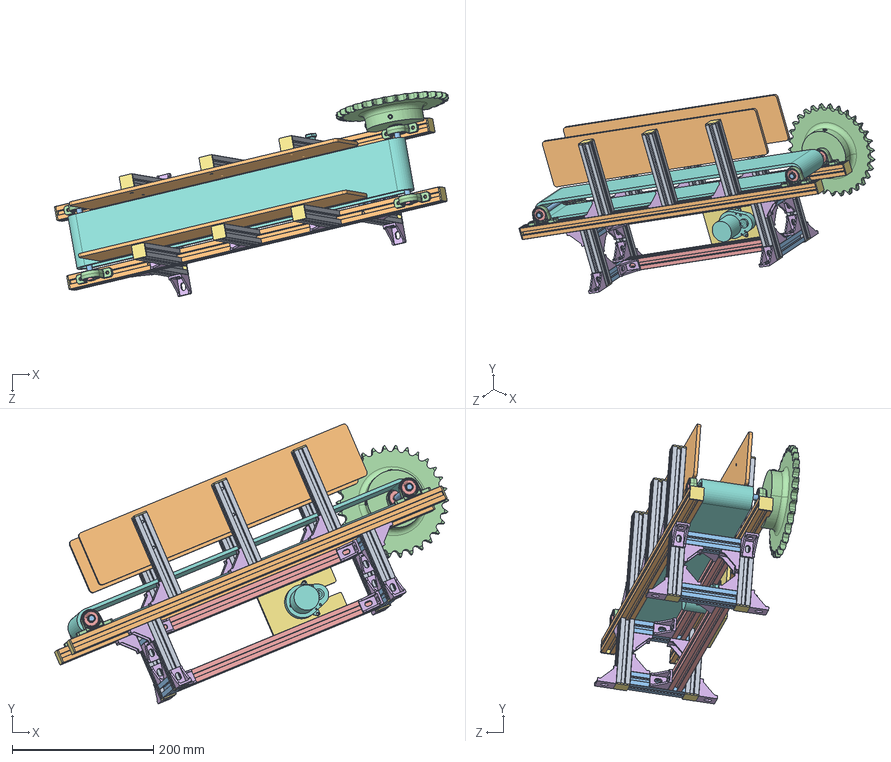
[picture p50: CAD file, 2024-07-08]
solidwork do an tot nghiep/bangtailon/Bangtai.SLDASM
557.0 x 395.7 x 289.8 mm
alluminum base 125mm x 6
alluminum base 585mm x 2
ty 10mm x 2
KP08 x 4
608RS x 4
alluminum angle corner joint x 26
nut_bit_thanhnhom x 14
Belt_49cm
alluminum base 100mm x 4
Tam_mi_ca 42x8 x 2
alluminum base 80mm x 4
sprocket50-z30.step
alluminum base 315_81mm x 2
bo nhom dinh hinh x 4
mica gan dong co dc
DC_motor ver2

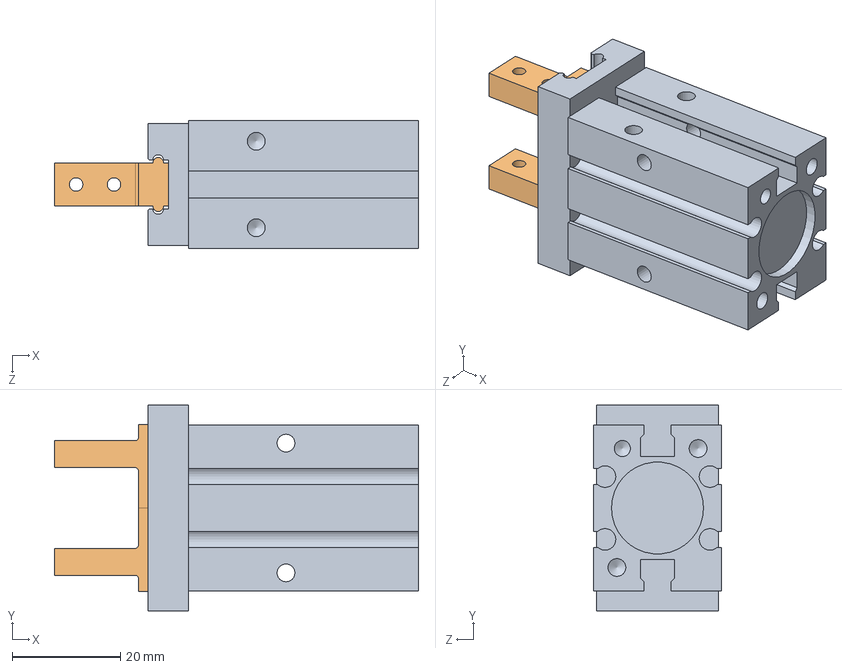
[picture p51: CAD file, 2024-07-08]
solidwork do an tot nghiep/bosung/SMC MHZ2-16.SLDASM
67.3 x 38.0 x 23.6 mm
SMC MHZ2-16 BODY
SMC MHZ2-16 GRIPPER x 2

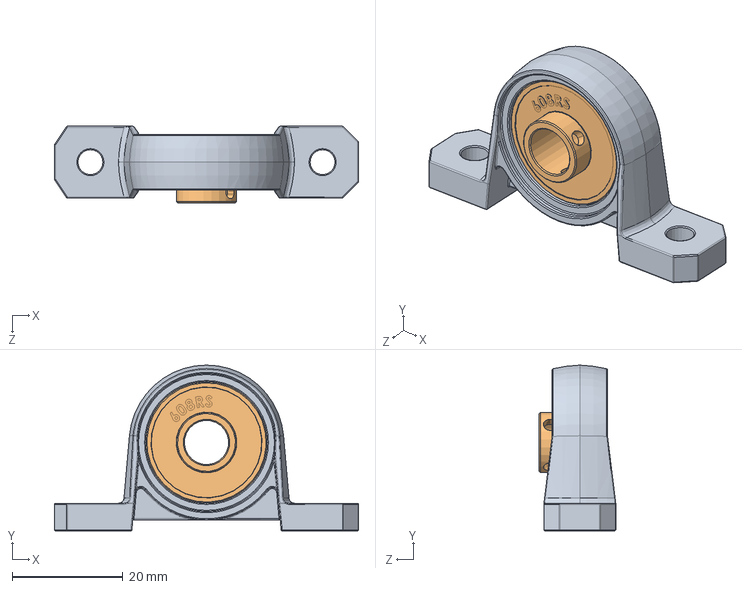
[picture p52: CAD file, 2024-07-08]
solidwork do an tot nghiep/bangtailon/KP08.SLDASM
55.0 x 30.0 x 13.9 mm
KP08
608RS

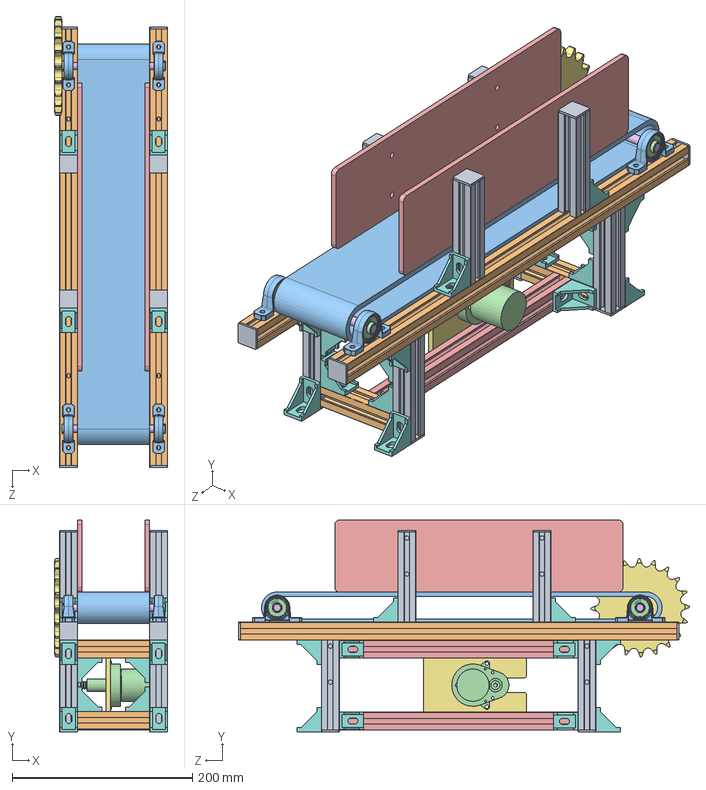
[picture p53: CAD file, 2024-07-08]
solidwork do an tot nghiep/Bangtai_nho/bangtai_nho.SLDASM
126.0 x 235.4 x 500.9 mm
alluminum base 100mm_1 x 8
alluminum base 485mm x 2
KP08 x 4
608RS x 4
Tam_mi_ca 32x8 x 2
ty 10mm x 2
Sprocket50-z20.step
alluminum angle corner joint x 24
nut_bit_thanhnhom x 12
alluminum base 80mm x 4
Belt_43cm
DC_motor ver2
alluminum base 264_91mm x 2
bo nhom dinh hinh x 4
mica gan dong co dc

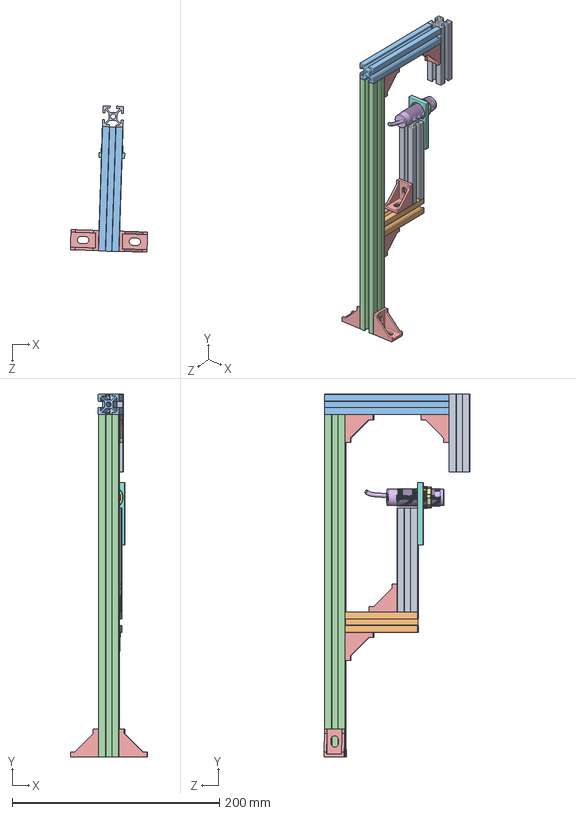
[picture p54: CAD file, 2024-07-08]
solidwork do an tot nghiep/Bom_nuoc_vao_chai/Gia_do_bomnuoc.SLDASM
74.6 x 350.0 x 141.2 mm
Alluminum base 7.5mm
Alluminum base 7mm
Alluminum base 12mm
Alluminum base 330mm
alluminum angle corner joint x 6
IR Sensor
Nut
gia_do_cam_bien
alluminum base 100mm

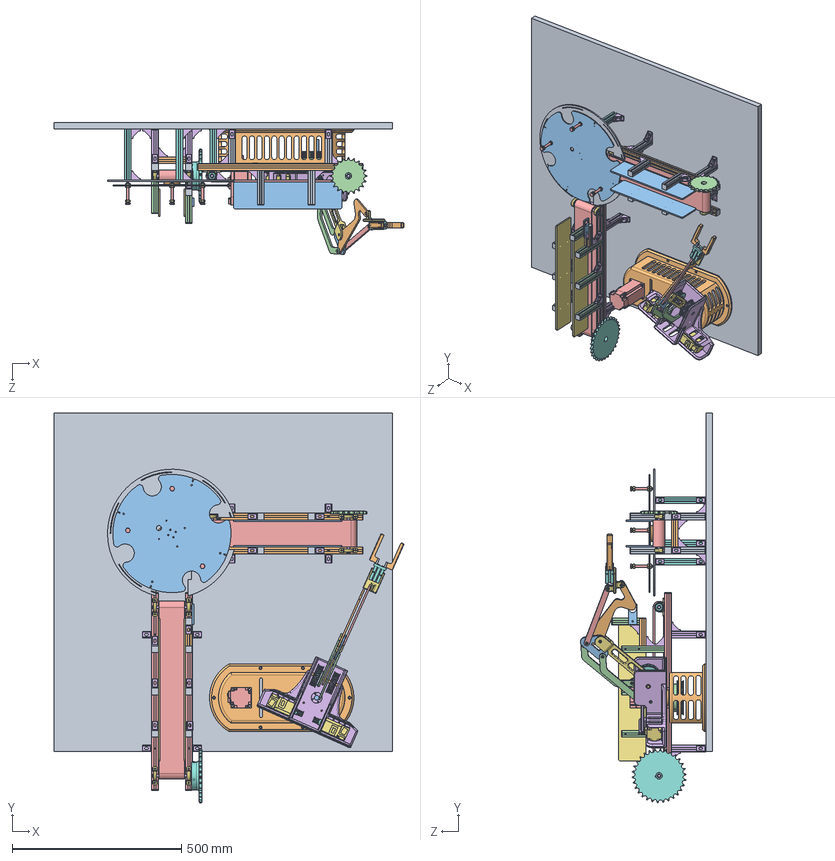
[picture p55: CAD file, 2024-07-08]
solidwork do an tot nghiep/assemble all.SLDASM
1033.2 x 1151.4 x 390.3 mm
de mam xoay mica ver 4
half of revolute joint x 4
dia mam xoay duoi
mat bich 8mm
bolt diameter 8mm length 6cm x 3
alluminum angle corner joint x 42
nut 8mm x 9
alluminum base 15mm x 3
base
Base_Magic ver 3
truc tron 14mm dai 10cm
pulley 60 rang truc 14mm
hf-kp23b_b
mat bich 14mm
hf-kp13_b.stp x 2
pulley 5M 10 rang truc 8mm x 2
bac dan 8mm x 4
truc 8mm dai 154mm
bac dan 3mm
alluminum base 125mm x 6
alluminum base 585mm x 2
ty 10mm x 4
KP08 x 8
608RS x 8
nut_bit_thanhnhom x 28
alluminum base 80mm x 5
gia_do_cam_bien
alluminum base 80mm cho cam bien
Belt_49cm
alluminum base 100mm x 4
Tam_mi_ca 42x8 x 2
sprocket50-z30.step
alluminum base 100mm_1 x 8
alluminum base 485mm x 2
Tam_mi_ca 32x8 x 2
Sprocket50-z20.step
Belt_43cm
pulley 40 rang truc 8mm khoang cach lo 12 mm
joint 2 magic ver 2
pulley 40 rang truc 13.8mm khoang cach truc 15mm
keo joint 3 ver 2
joint 3 ver 2
quan xi ver 3
thanh ngang 191mm ver 2 x 2
thanh ngang 191mm
Joint1_Magic ver5
join4 ver2
SMC MHZ2-16 BODY
SMC MHZ2-16 GRIPPER x 2
gripper x 2

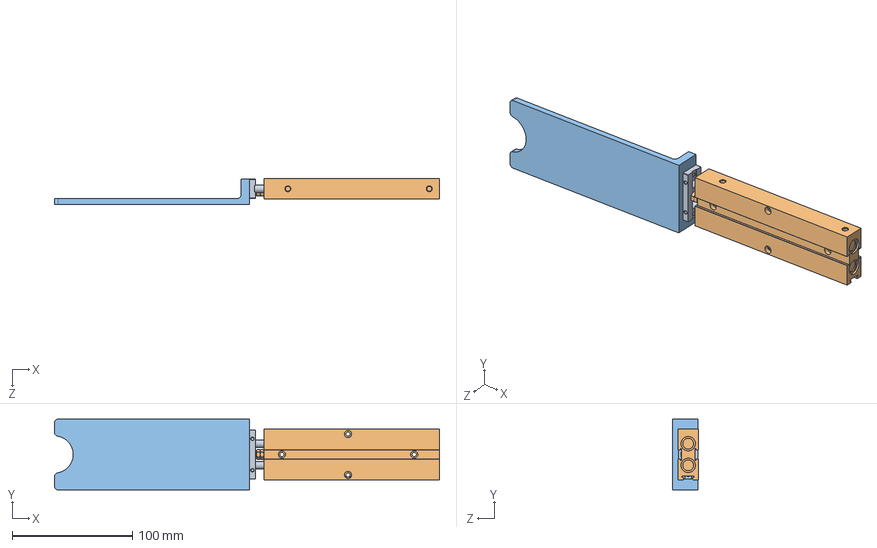
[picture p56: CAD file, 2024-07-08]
solidwork do an tot nghiep/TN10X100S(0)+().sldasm
320.0 x 59.0 x 21.5 mm
TN10-100_fp
TN10-100 - 100_b
mieng day nap chai

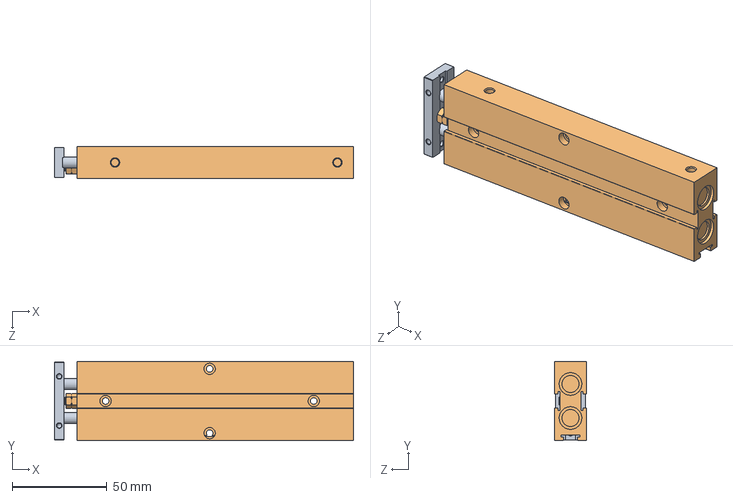
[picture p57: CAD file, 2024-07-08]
solidwork do an tot nghiep/xy lanh doi.SLDASM
158.0 x 42.0 x 17.0 mm
TN10-100_fp
TN10-100 - 100_b

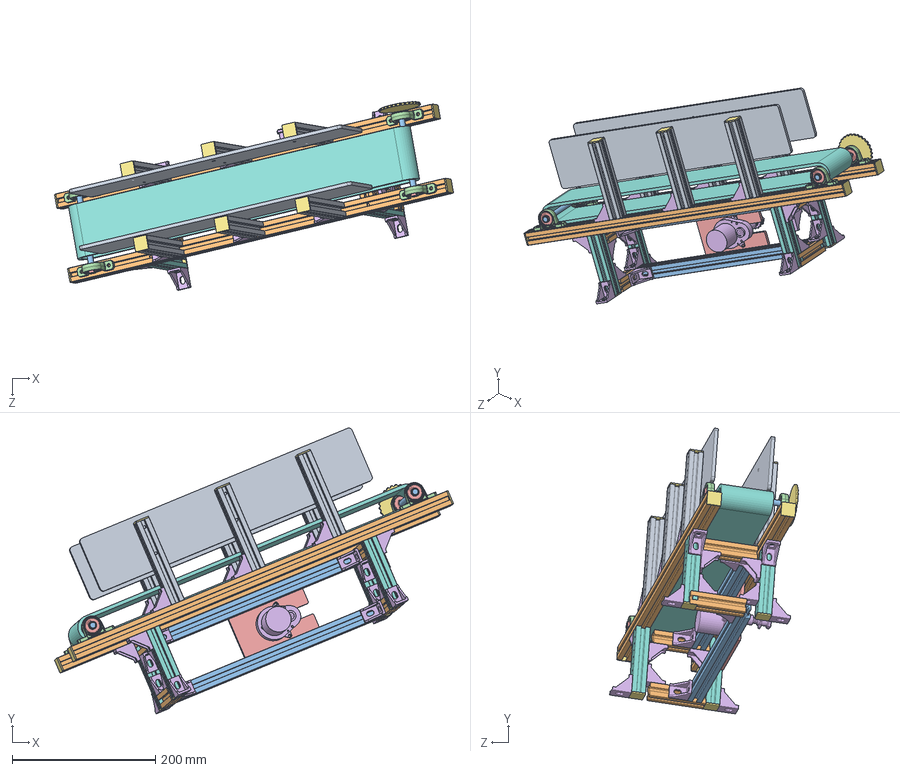
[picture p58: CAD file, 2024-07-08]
solidwork do an tot nghiep/Bangtai.SLDASM
556.3 x 398.6 x 263.1 mm
alluminum base 125mm x 6
alluminum base 585mm x 2
ty 10mm x 2
KP08 x 4
608RS x 4
alluminum angle corner joint x 26
nut_bit_thanhnhom x 14
Belt_49cm
Tam_mi_ca 42x8 x 2
alluminum base 80mm x 4
alluminum base 315_81mm x 2
bo nhom dinh hinh x 4
mica gan dong co dc
DC_motor ver2
Bánh_răng_xích
Alluminum base 100mm x 4

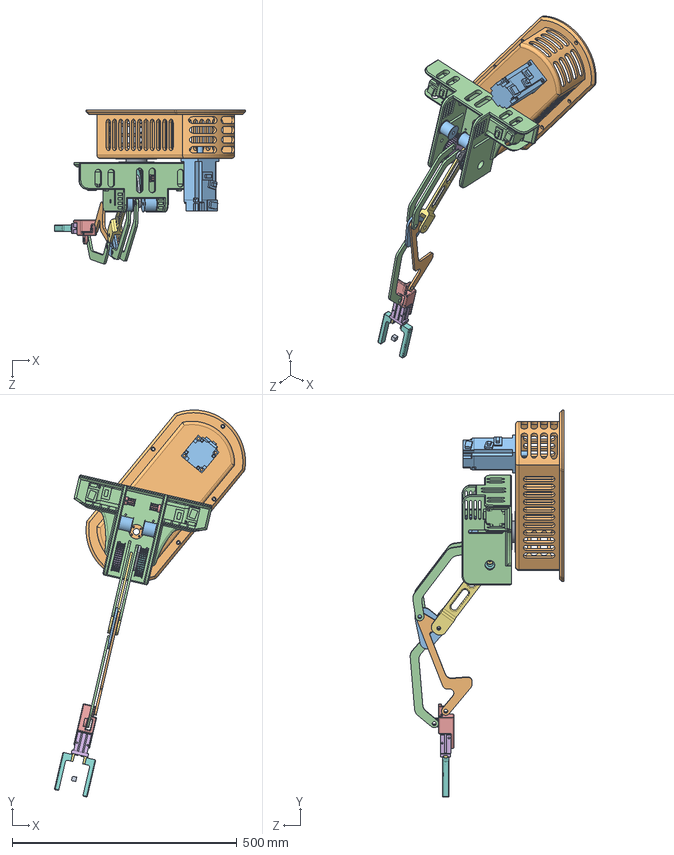
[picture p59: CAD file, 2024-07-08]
solidwork do an tot nghiep/assemble_robot_simulation.SLDASM
424.7 x 860.3 x 341.6 mm
half of revolute joint x 2
Base_Magic ver 3
hf-kp23b_b
hf-kp13_b.stp x 2
pulley 5M 10 rang truc 8mm x 2
pulley 40 rang truc 8mm khoang cach lo 12 mm
joint 2 magic ver 2
pulley 40 rang truc 13.8mm khoang cach truc 15mm
keo joint 3 ver 2
joint 3 ver 2
quan xi ver 3
thanh ngang 191mm ver 2 x 3
join4 ver2
SMC MHZ2-16 BODY
SMC MHZ2-16 GRIPPER x 2
gripper x 2
end manipulator
mat bich 14mm
puly cang dai 5m x 2
Joint1_Magic ver9

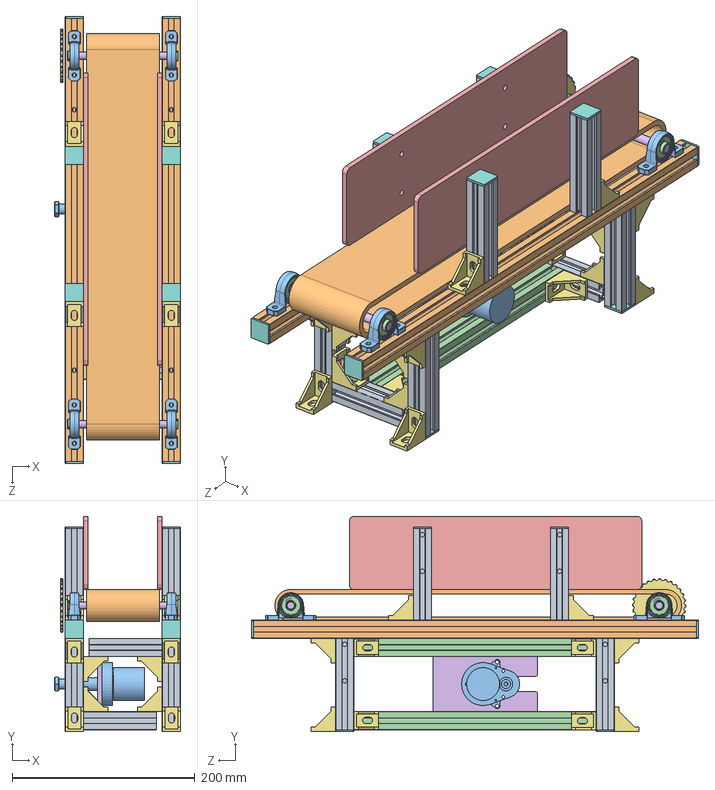
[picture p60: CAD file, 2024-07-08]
solidwork do an tot nghiep/bangtai_nho.SLDASM
137.9 x 235.4 x 489.0 mm
alluminum base 100mm_1 x 8
alluminum base 485mm x 2
KP08 x 4
608RS x 4
Tam_mi_ca 32x8 x 2
ty 10mm x 2
alluminum angle corner joint x 24
nut_bit_thanhnhom x 12
alluminum base 80mm x 4
Belt_43cm
DC_motor ver2
alluminum base 264_91mm x 2
bo nhom dinh hinh x 4
mica gan dong co dc
Bánh_răng_xích

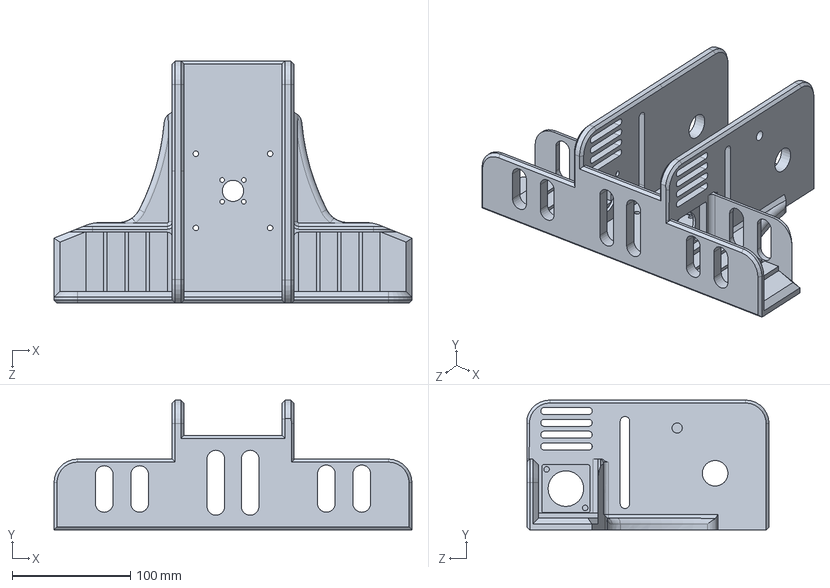
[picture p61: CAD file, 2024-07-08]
solidwork do an tot nghiep/joint1 ver 10.SLDASM
303.0 x 110.0 x 205.0 mm

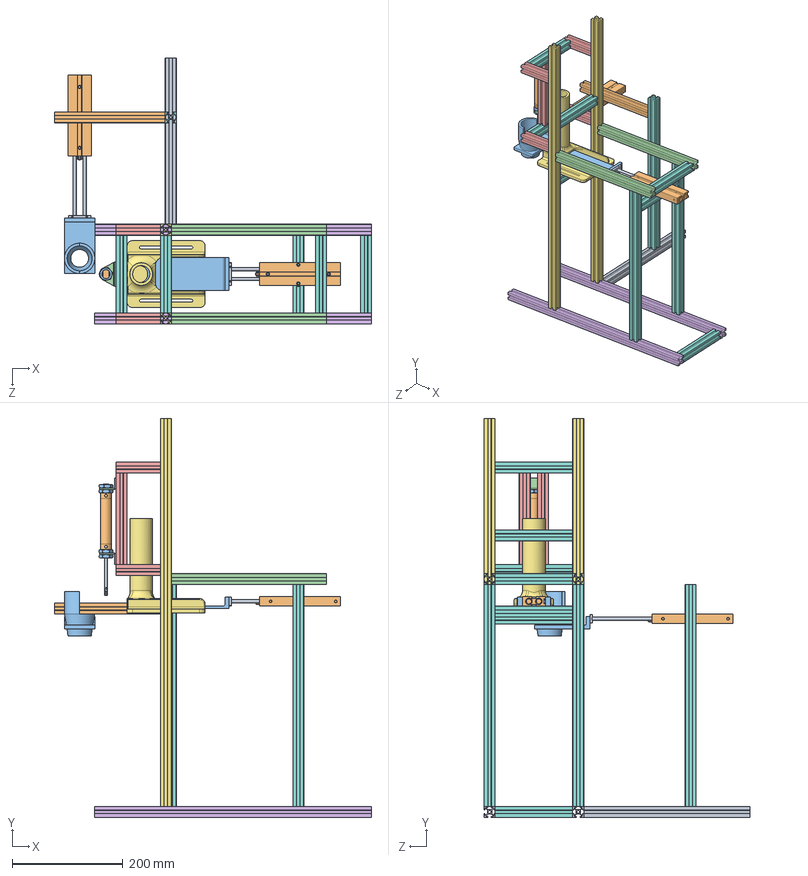
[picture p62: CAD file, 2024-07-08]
solidwork do an tot nghiep/xi lanh khi nen.SLDASM
572.7 x 720.1 x 480.1 mm
CILINDRO-16X100-CA
MAL 16X100-CA
nut for pneumatic cylinder x 4
Cylinder_holder x 2
alluminum base 165mm x 2
bo nhom dinh hinh x 7
mieng de nap chai
alluminum base 140mm x 7
TN10-100_fp x 2
TN10-100 - 100_b x 2
mieng day nap chai
alluminum base 280mm x 2
alluminum base 80mm x 4
Alluminum base 500mm x 2
alluminum base 700mm x 2
alluminum base 400mm x 3
alluminum base 300mm
alluminum base 200mm
pheu rot nap chai

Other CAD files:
solidwork do an tot nghiep/Bangtai_nho/KP08.SLDASM
solidwork do an tot nghiep/608RS.SLDPRT
solidwork do an tot nghiep/Alluminum base 100mm.SLDPRT
solidwork do an tot nghiep/Alluminum base 12.5mm.SLDPRT
solidwork do an tot nghiep/Alluminum base 12mm.SLDPRT
solidwork do an tot nghiep/Alluminum base 330mm.SLDPRT
solidwork do an tot nghiep/Alluminum base 500mm.SLDPRT
solidwork do an tot nghiep/Alluminum base 7.5mm.SLDPRT
solidwork do an tot nghiep/Alluminum base 760mm.SLDPRT
solidwork do an tot nghiep/Alluminum base 7mm.SLDPRT
solidwork do an tot nghiep/Bangtai_nho/608RS.SLDPRT
solidwork do an tot nghiep/Bangtai_nho/Belt_43cm.SLDPRT
solidwork do an tot nghiep/Bangtai_nho/KP08.SLDPRT
solidwork do an tot nghiep/Bangtai_nho/Sprocket50-z20.step
solidwork do an tot nghiep/Bangtai_nho/Tam_mi_ca 32x8.SLDPRT
solidwork do an tot nghiep/Bangtai_nho/alluminum angle corner joint.SLDPRT
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

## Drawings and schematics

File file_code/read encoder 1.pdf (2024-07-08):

## Totally Integrated Automation Portal

# fix_plc / PLC_1 [CPU 1214C DC/DC/DC] / Program blocks

# read encoder 1 [FC1]

## read encoder 1 Properties General

Name | read encoder 1 | Number | 1 | Type | FC | Language | LAD
Numbering | Automatic

## Information

Title | | Author | Comment | Family
Version | 0.1 | User-defined ID

## read encoder 1

Name | Data type | Default value | Comment

## Input Output InOut Temp Constant Return

read encoder 1 | Void

# Network 1:

## Automation Portal

## Network 1: (1.1 / 11.1) N

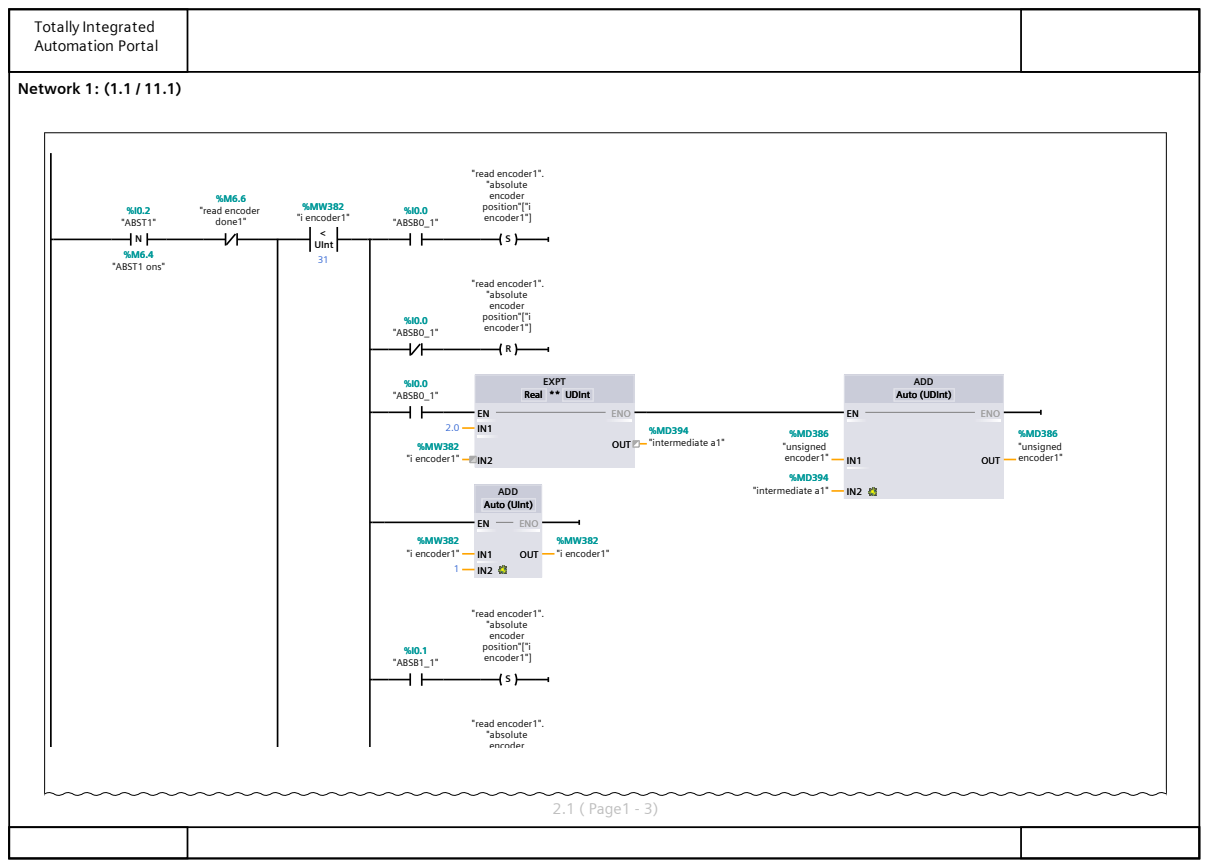
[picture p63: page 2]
UInt <; EXPT; Real ** UDInt; ADD; Auto (UDInt) ADD; Auto (UInt); "ABST1"; "ABST1 ons"; "read encoder done1"; "i encoder1"; "ABSB0_1"; "read encoder1". "absolute encoder position"["i encoder1"]; "intermediate a1"; "unsigned encoder1"; "ABSB1_1"; "read encoder1". "absolute encoder; ENO; OUT; 2.1 ( Page1 - 3)

Auto (UDInt) EN
Auto (UInt) EN

## Automation Portal

## Network 1: (2.1 / 11.1)

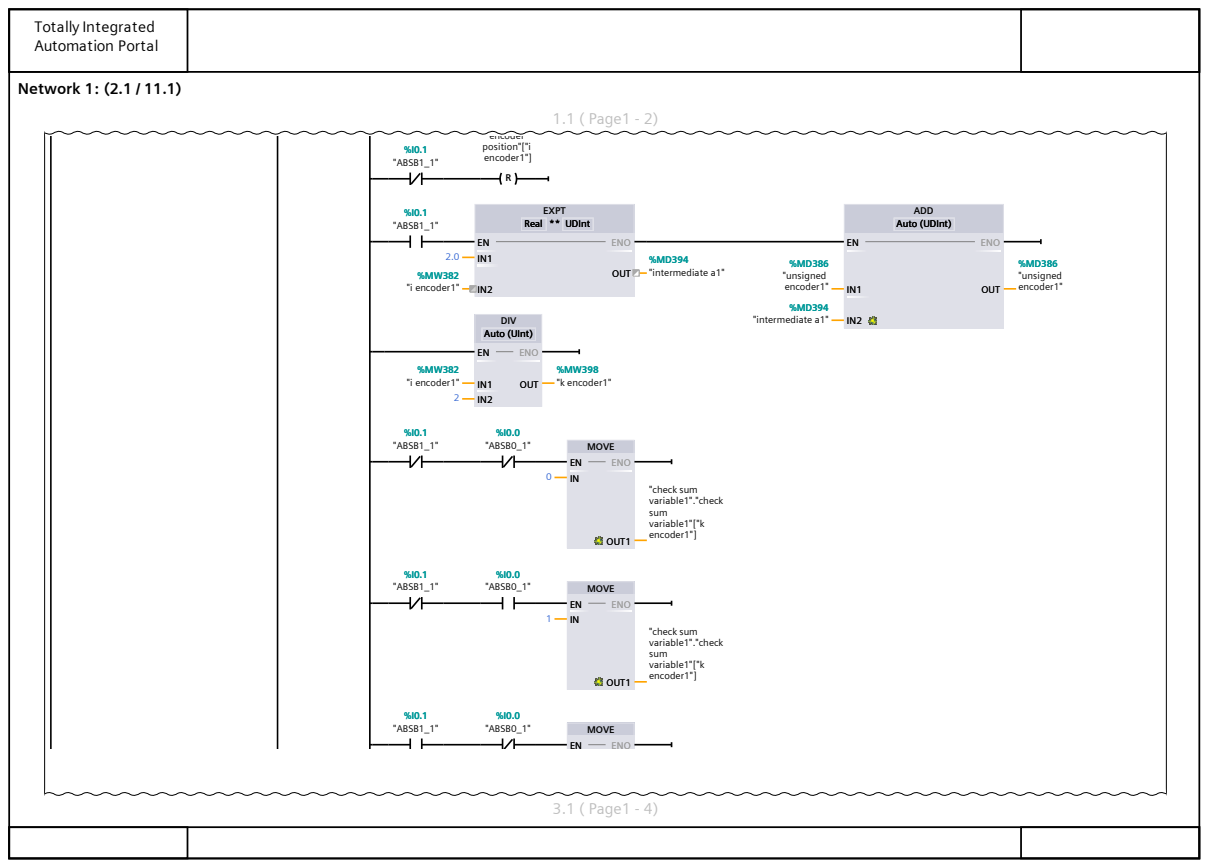
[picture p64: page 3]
1.1 ( Page1 - 2) R; EXPT; Real ** UDInt; ADD; Auto (UDInt) DIV; Auto (UInt); MOVE; "ABSB1_1"; encoder position"["i; encoder1"]; "i encoder1"; "intermediate a1"; "unsigned encoder1"; "k encoder1"; "ABSB0_1"; "check sum variable1"."check sum variable1"["k; ENO; OUT; Auto (UDInt) EN; OUT1; 3.1 ( Page1 - 4)

Auto (UDInt) EN

## Automation Portal

## Network 1: (3.1 / 11.1)

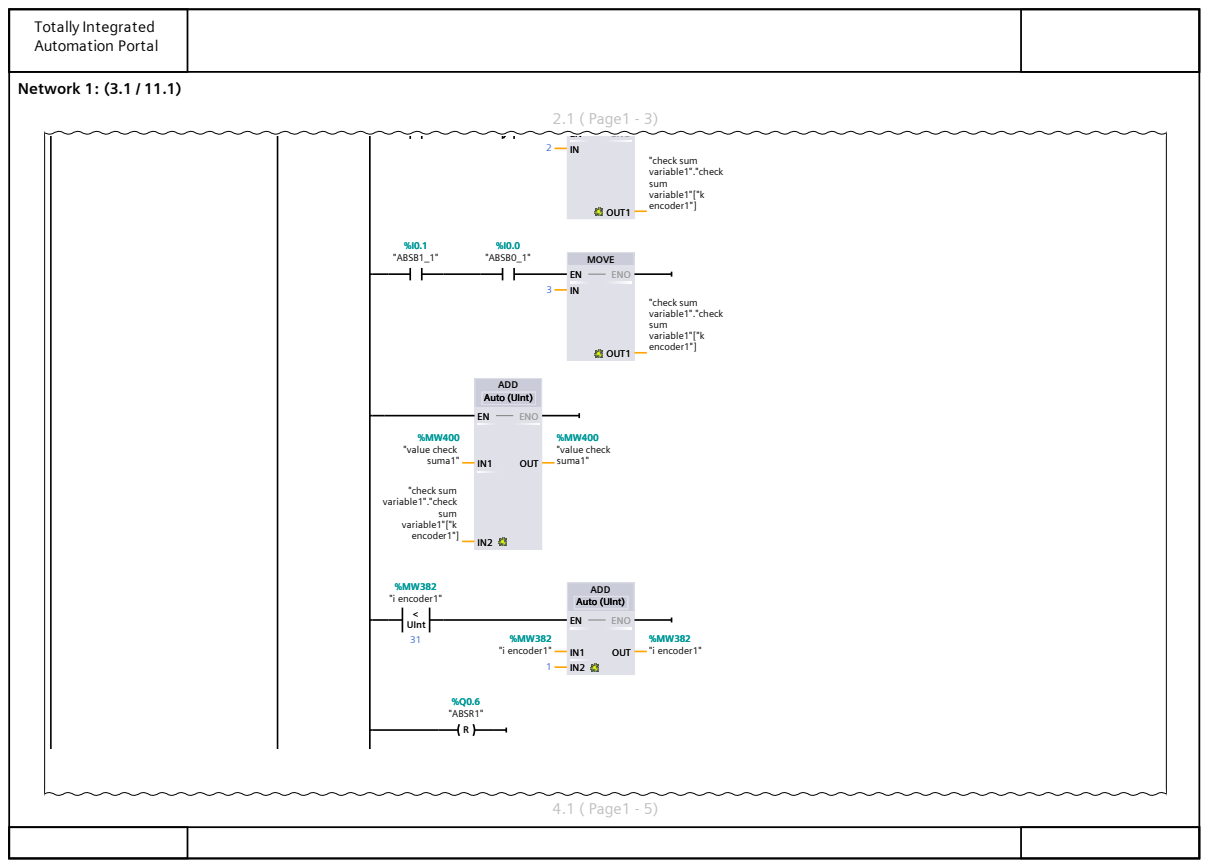
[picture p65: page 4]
2.1 ( Page1 - 3); MOVE ADD; Auto (UInt) UInt <; ADD; Auto (UInt) R; "check sum variable1"."check sum variable1"["k; encoder1"]; "ABSB1_1"; "ABSB0_1"; "value check suma1"; "i encoder1"; "ABSR1"; ENO; OUT1; OUT; Auto (UInt); 4.1 ( Page1 - 5)

## Automation Portal

## Network 1: (4.1 / 11.1)

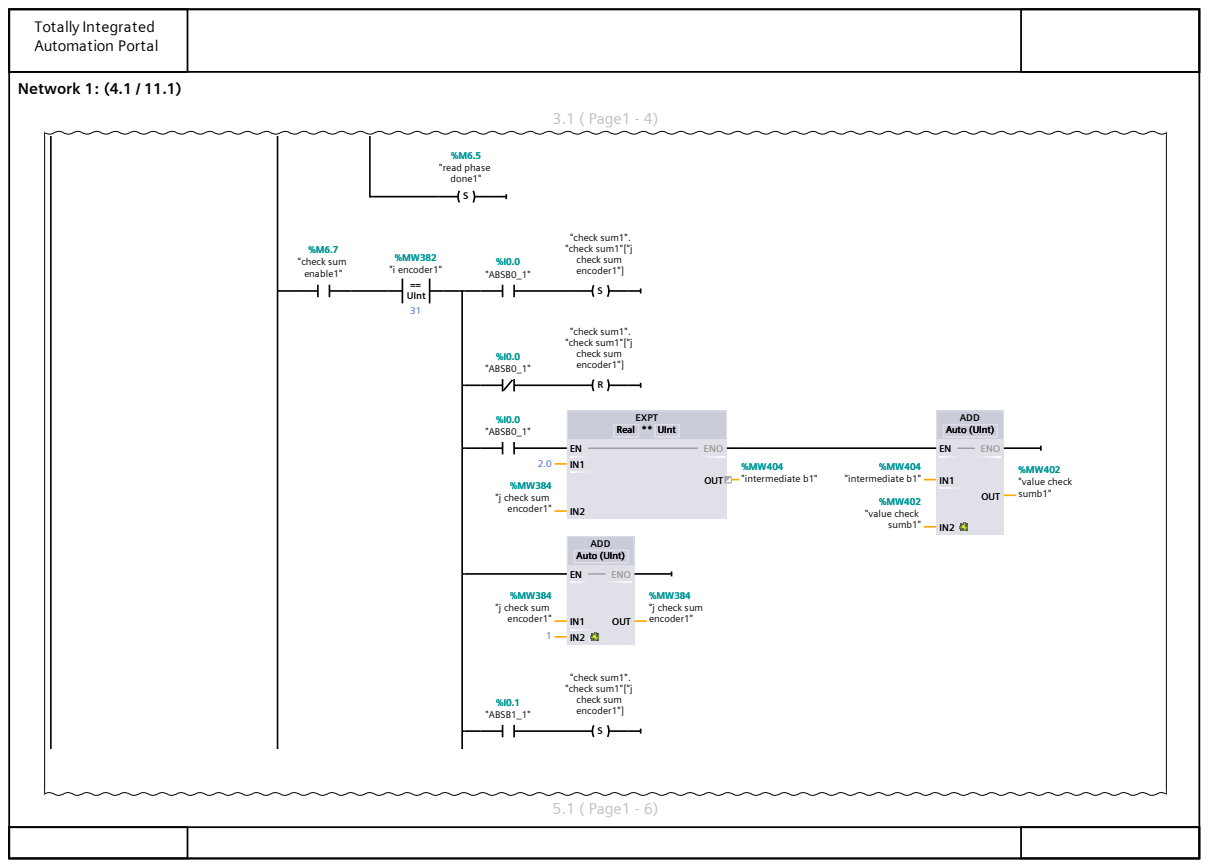
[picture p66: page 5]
3.1 ( Page1 - 4) UInt ==; EXPT; Real ** UInt; ADD; Auto (UInt) ADD; Auto (UInt); "check sum enable1"; "i encoder1"; "ABSB0_1"; "check sum1". "check sum1"["j check sum encoder1"]; "j check sum encoder1"; "intermediate b1"; "value check sumb1"; "ABSB1_1"; "read phase done1"; ENO; OUT; Auto (UInt) EN IN1; 5.1 ( Page1 - 6)

Auto (UInt) EN

## Automation Portal

## Network 1: (5.1 / 11.1)

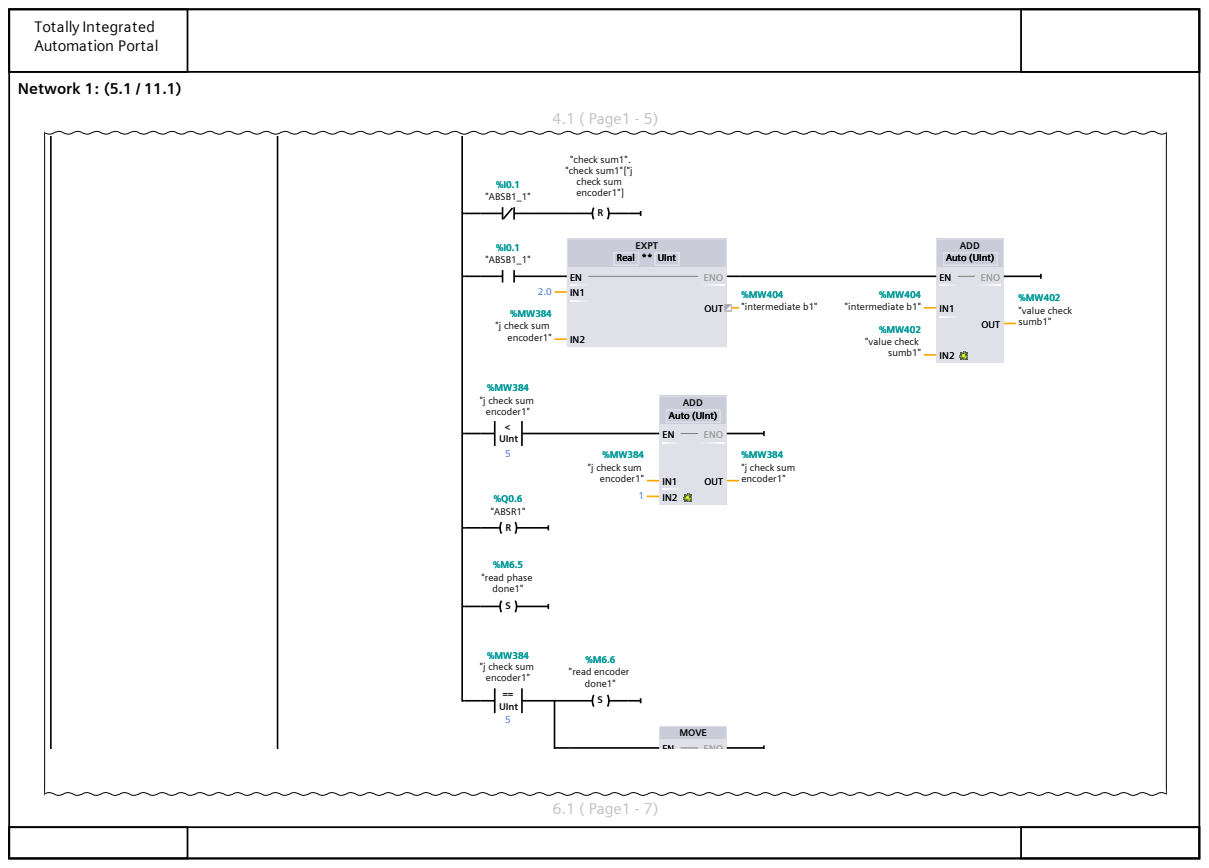
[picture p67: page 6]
4.1 ( Page1 - 5) R; EXPT; Real ** UInt; ADD; Auto (UInt) UInt <; Auto (UInt) R; SUInt ==; MOVE; "ABSB1_1"; "check sum1". "check sum1"["j check sum encoder1"]; "j check sum encoder1"; "intermediate b1"; "value check sumb1"; "ABSR1"; "read phase done1"; "read encoder done1"; ENO; OUT; Auto (UInt); 6.1 ( Page1 - 7)

Auto (UInt) EN

## Automation Portal

## Network 1: (6.1 / 11.1)

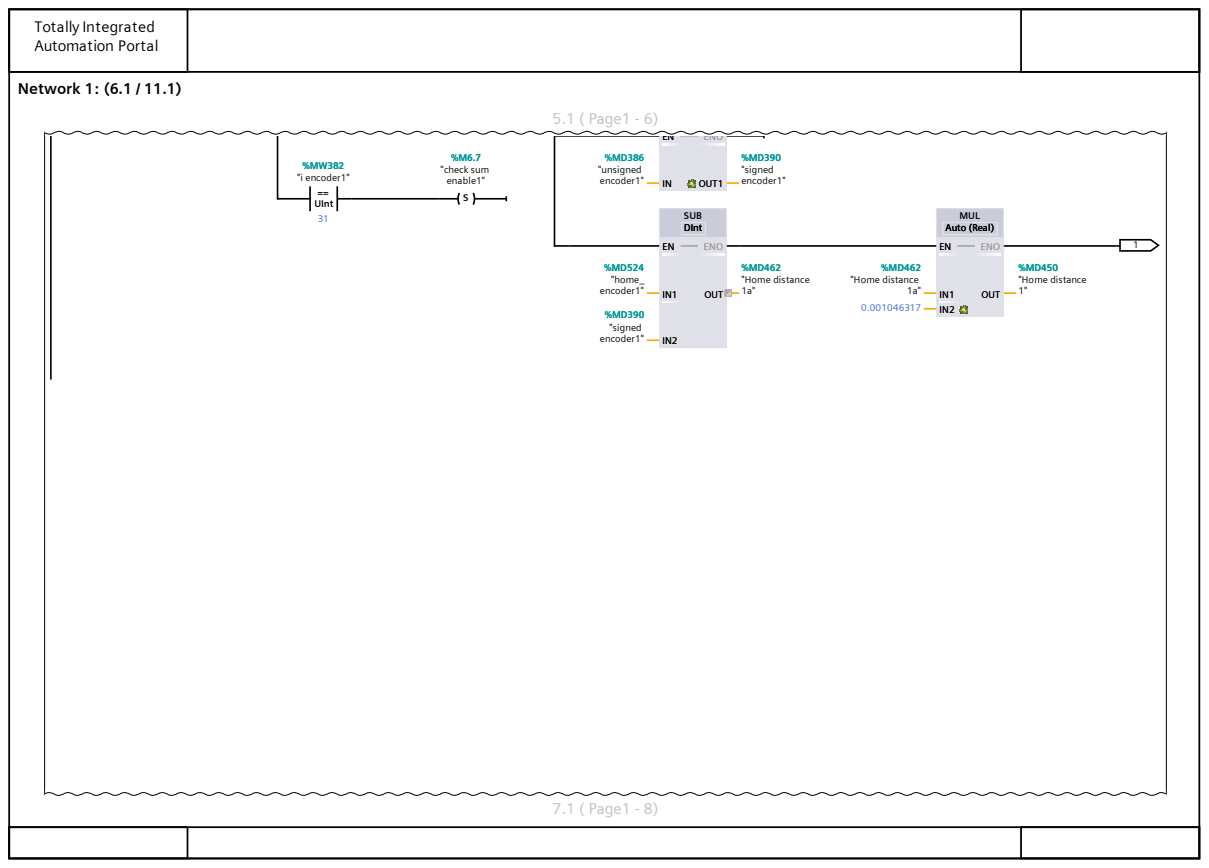
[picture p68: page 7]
5.1 ( Page1 - 6); SUB DInt; MUL Auto (Real) UInt ==; "unsigned encoder1"; "signed encoder1"; "home_ encoder1"; "Home distance 1a"; "Home distance 1"; "i encoder1"; "check sum enable1"; ENO; OUT1; OUT DInt; OUT; Auto (Real); 7.1 ( Page1 - 8)

Auto (Real) EN

## Automation Portal

## Network 1: (7.1 / 11.1)

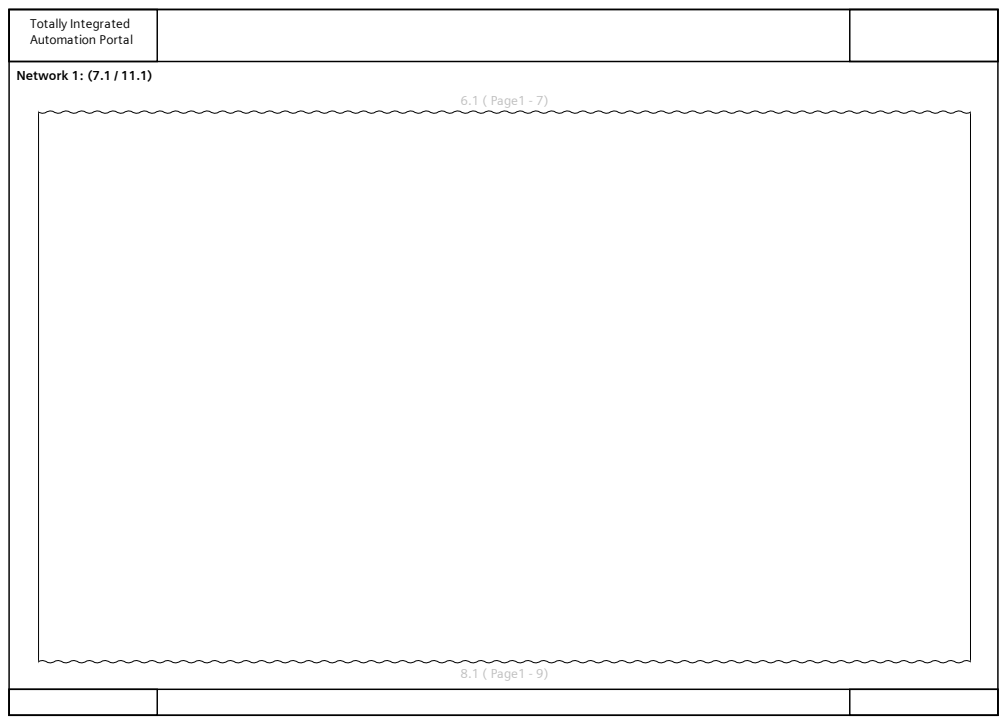
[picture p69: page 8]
6.1 ( Page1 - 7); 8.1 ( Page1 - 9)

## Automation Portal

## Network 1: (8.1 / 11.1)

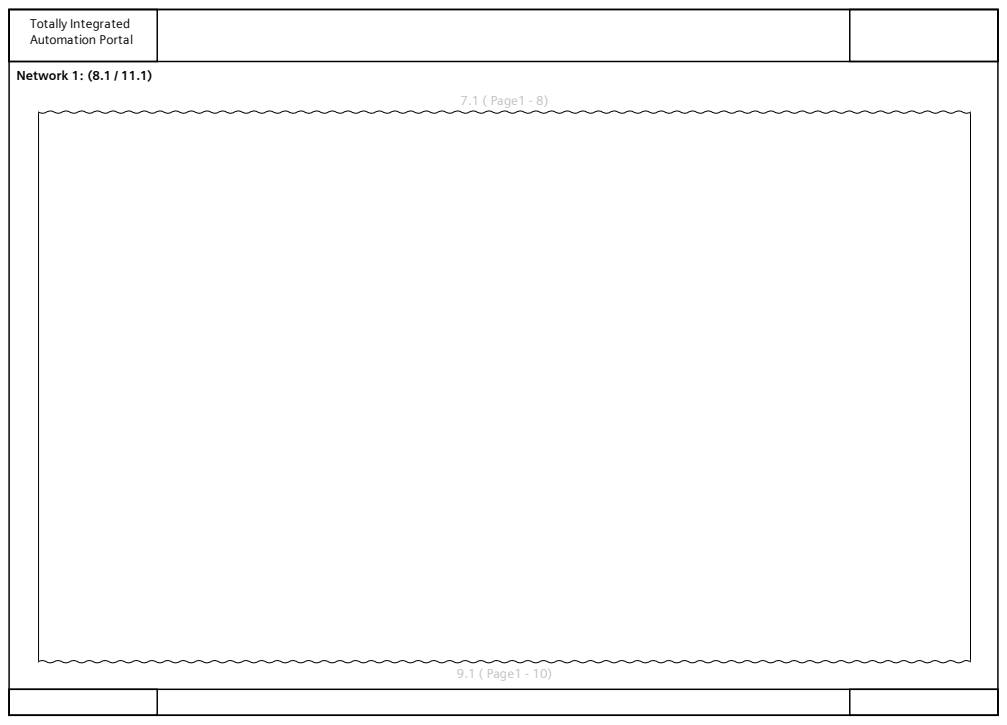
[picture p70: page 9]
7.1 ( Page1 - 8); 9.1 ( Page1 - 10)

## Automation Portal

## Network 1: (9.1 / 11.1)

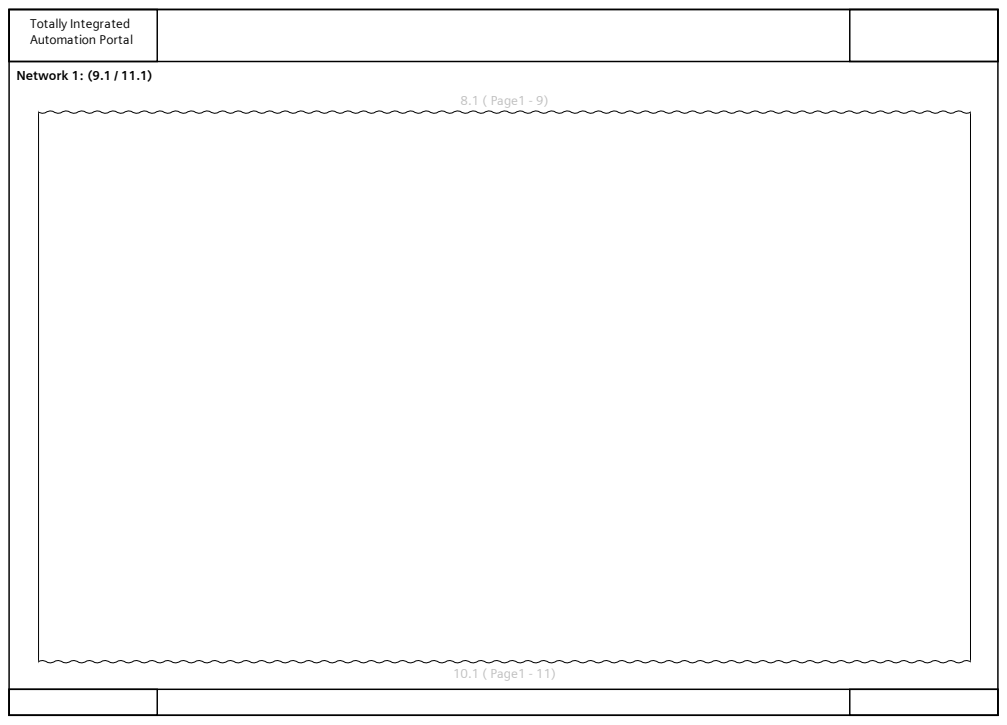
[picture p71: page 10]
8.1 ( Page1 - 9); 10.1 ( Page1 - 11)

## Automation Portal

## Network 1: (10.1 / 11.1)

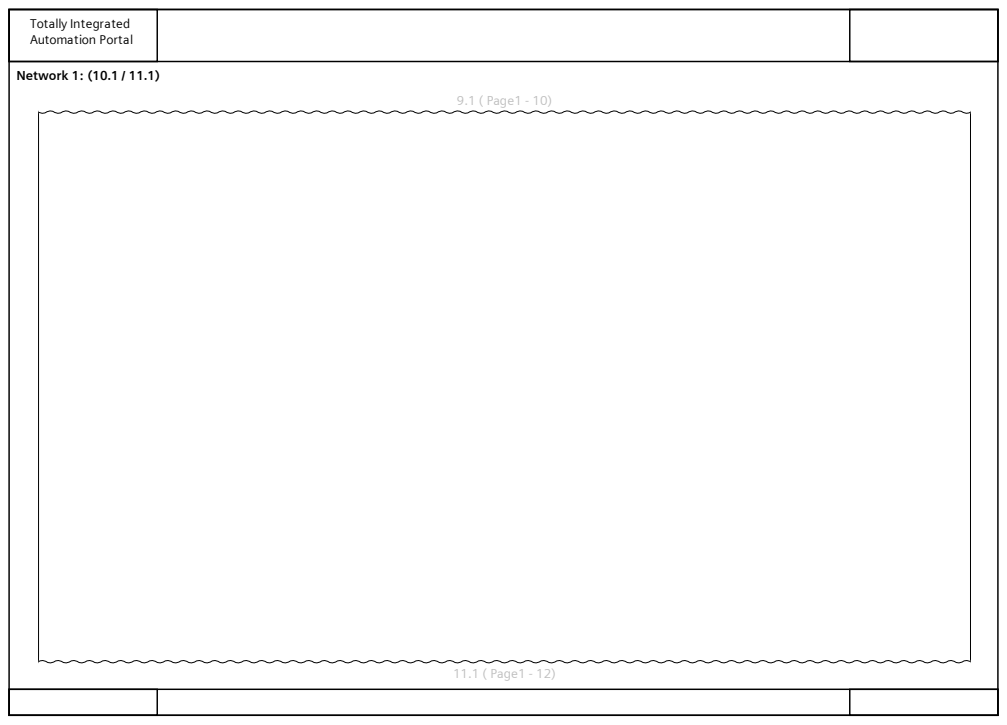
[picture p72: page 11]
9.1 ( Page1 - 10); 11.1 ( Page1 - 12)

## Automation Portal

## Network 1: (11.1 / 11.1)

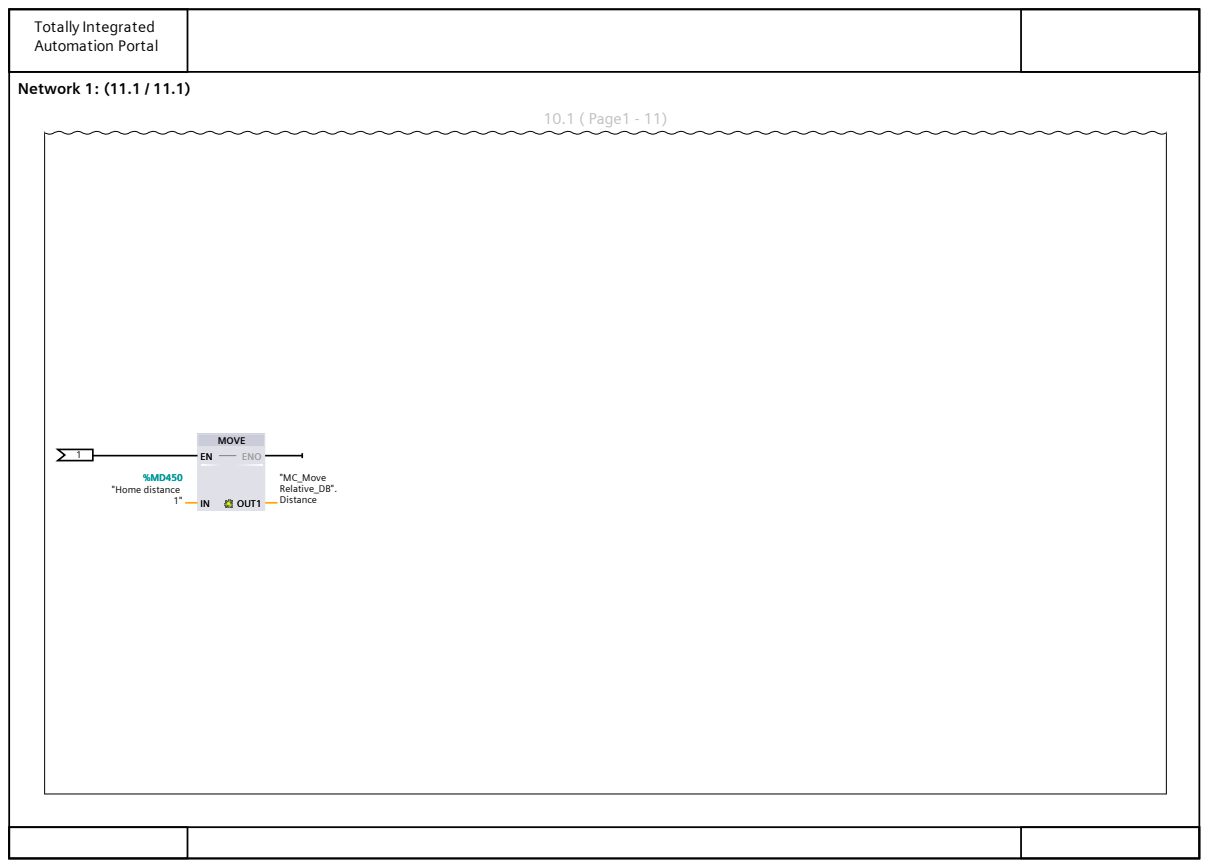
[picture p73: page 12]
10.1 ( Page1 - 11); MOVE 1; "Home distance 1"; "MC_Move; Relative_DB".; Distance EN; ENO; OUT1

## Automation Portal

# Network 2:

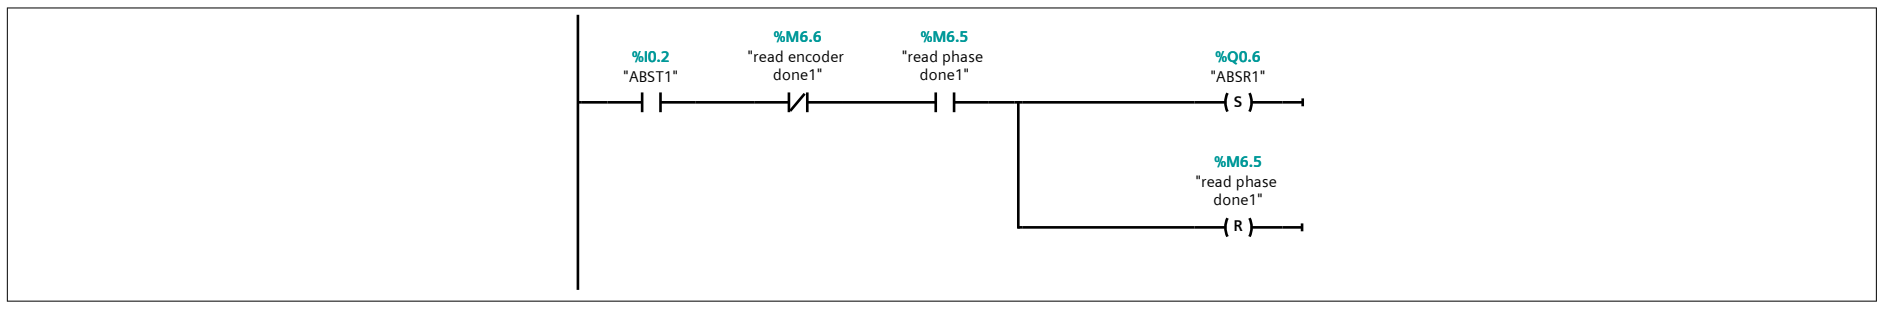
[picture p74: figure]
"ABST1"; "read encoder; done1"; "read phase done1"; "ABSR1"
Network 3:; UInt ==; "i encoder1"; "j check sum encoder1"; "read encoder done1"; "ABSR1"; "read home; done1"
